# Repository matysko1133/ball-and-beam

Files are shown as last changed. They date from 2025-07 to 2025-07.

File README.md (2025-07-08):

> # Ball and Beam PID Controller
> Bachelor thesis - Positioning a Ball on an Inclined Beam Using Scilab Software
>
> The subject of this bachelor thesis is the design and implementation of a ball and inclined beam system using the Arduino UNO platform, an infrared ToF distance sensor and a servo actuator. The objective was to develop a control system that applies the principles of feedback control to ensure accurate and stable positioning of the ball through the controller’s control variable. The solution included the construction of the mechanical setup, system identification, synthesis and implementation of the PID controller in the Scilab environment and its interfacing with hardware components. The thesis also documents the design of ideal construction parts and the selection of a suitable ball. Based on experimental measurements, a mathematical model was created and the PID controller parameters were determined. The control algorithm was implemented on a physical system that initially exhibited unsatisfactory behavior. Therefore, the controller parameters were adjusted and finetuned again using the mathematical model.
>
> ## Startup guide
> This document serves as a guide to running simulations, whether with a model or with a real system. Certain steps are identical in both cases. It is necessary to have the necessary development environment **Arduino IDE (version 2.3.3)** and **Scilab software (version 2024.1.0)**. All scripts and simulation schemes that are necessary for the simulation alternative are attached in files.
> 
>> ### Running a simulation on the model
>>  To start a simulation with the model, it is necessary to load the parameters of the system and the PID controller.
>> Run the script *PID_parameters.sci*. After this step, in the file named
>> *model_PID_controller.zcos* just start the simulation by pressing the "Start" button, which is located
>> in the top bar of the window under the white arrow icon. After the simulations are finished, another click will appear on the screen
>> two windows with time courses of the measured quantities will appear. However, these waveforms can be displayed more clearly by running the script *model_plotter.sci*. The script
>> adds grids in the graphic outputs for better identification of critical points and legends describing individual.
> 
>> ### Running the simulation on a real system
>> Running on a real system includes specific steps that are required before the actual run. A special requirement is to upload the *toolbox_arduino_v5.ino* code to the Arduino UNO
>> board via the Arduino IDE environment. Without this script, it is not possible to establish the communication between Arduino and Scilab.
>> Equally important is the correct connection of the hardware components, specifically connecting the ToF sensor pin **SDA to the Arduino pin A4**, the **SCL pin to the A5 pin** and >> **the servo motor pin for the control signal (in our case the orange cable) to the Arduino digital pin
>> ~9 supporting PWM**. Since *toolbox_ardino_v5.ino* works with servomotor pins 9 and 10, it is possible to use the control signal also on pin 10, then it is necessary to be able to >> specify this change in the simulation scheme in the block **"Servo WRITE"** (1 represents pin 9, 2 represents pin 10). Finally, the key connection between the PC and Arduino is a
>> USB cable on the correct port, which is specified in Scilab by the **ARDUINO_SETUP** block. To identify the currently connected COM port, it is best to use the Arduino platform IDE: >> *Tools -> "Port: COMX"*, or a direct listing in the bottom bar of the window. After these steps, the simulation *real_system_PID_controller.zcos* is started in the same way as model >> simulation, while the time course of the measured quantities changes in real time. However, if for some reason the user wants to plot the data after the simulation is finished, they >> can do so using the *real_system_plotter.sci* script.

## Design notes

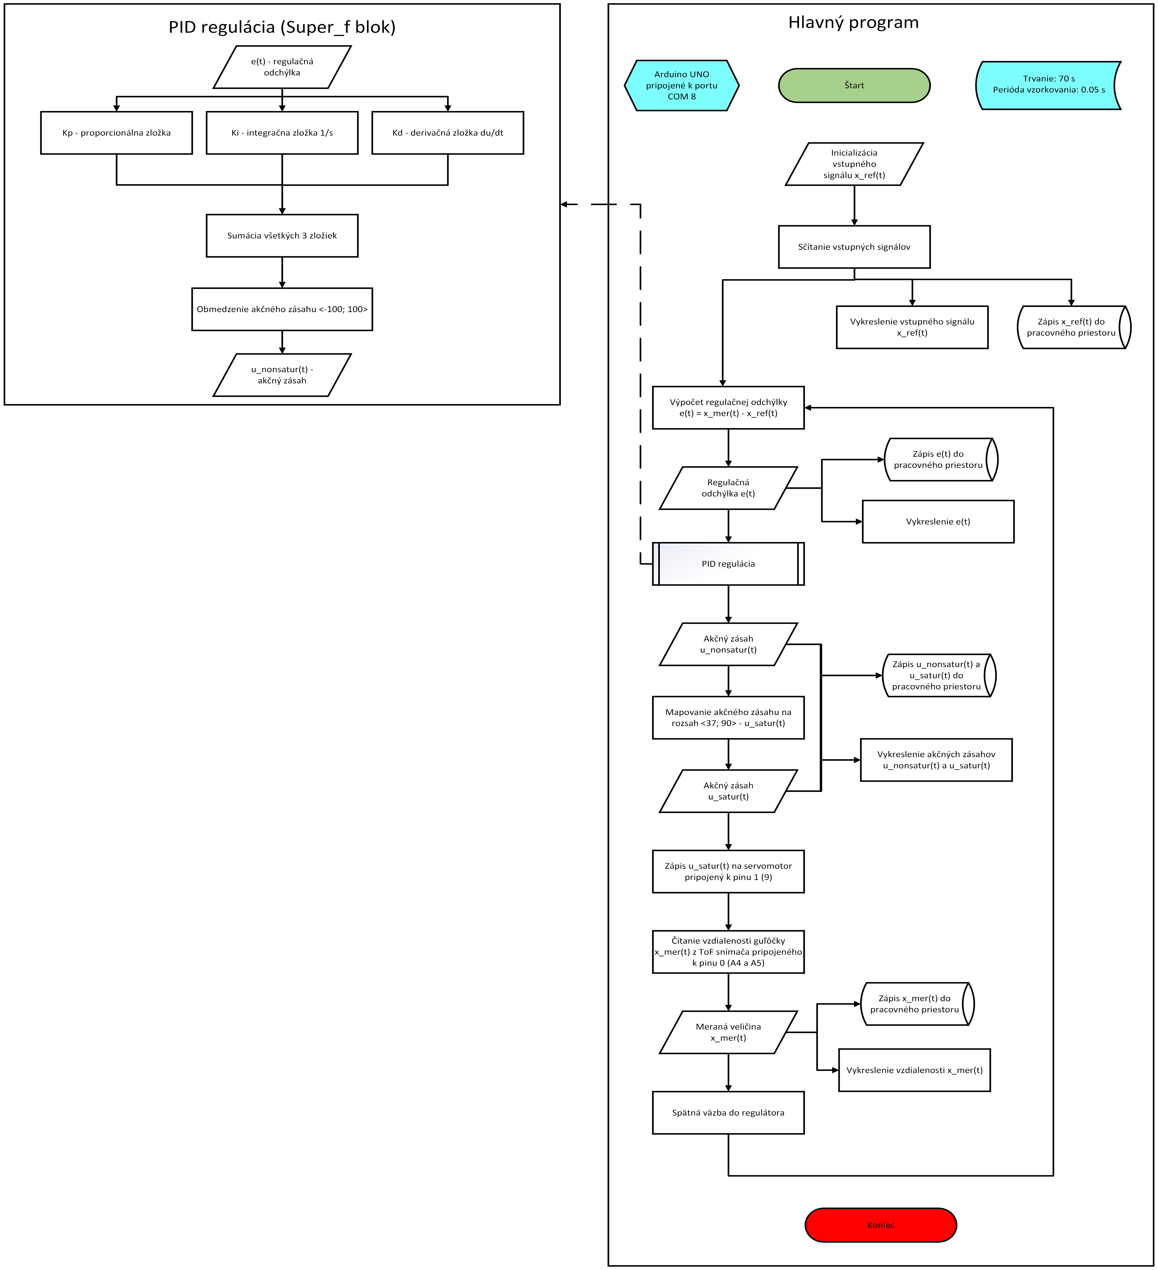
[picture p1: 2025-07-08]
flowchart.png

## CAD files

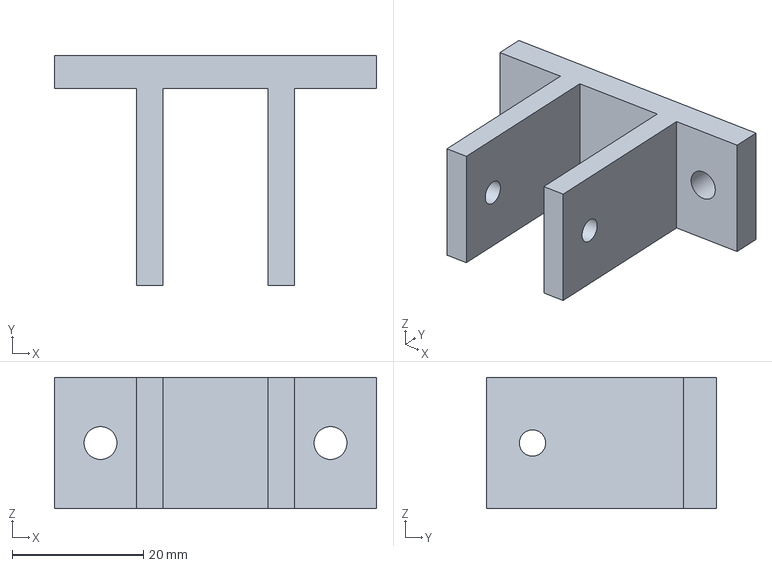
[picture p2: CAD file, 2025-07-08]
Construction/Part_4_top.FCStd
49.0 x 35.0 x 20.0 mm

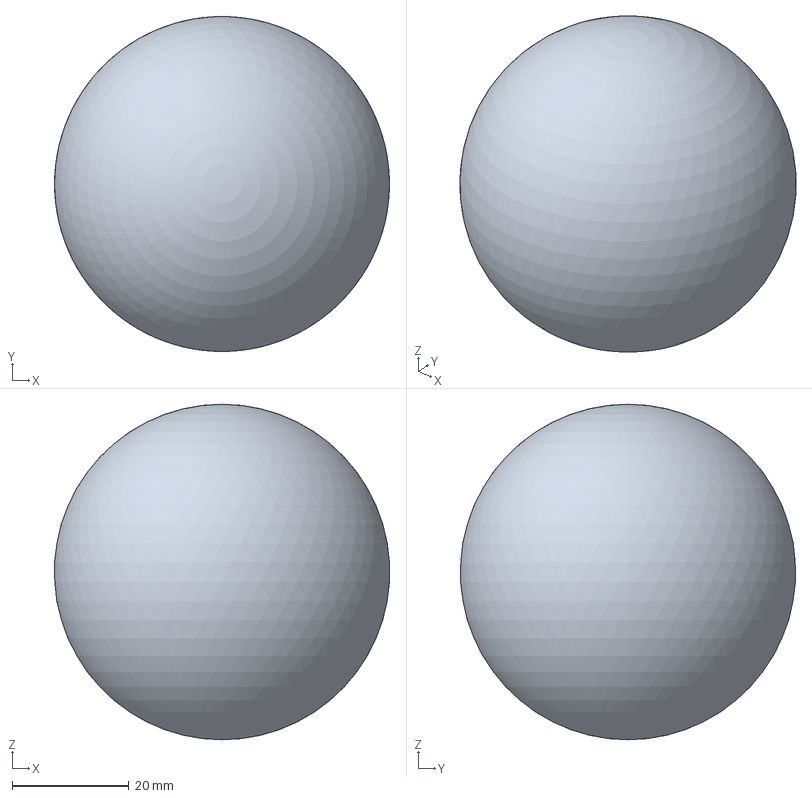
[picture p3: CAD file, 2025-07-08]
Construction/ball.FCStd
57.4 x 57.4 x 57.5 mm

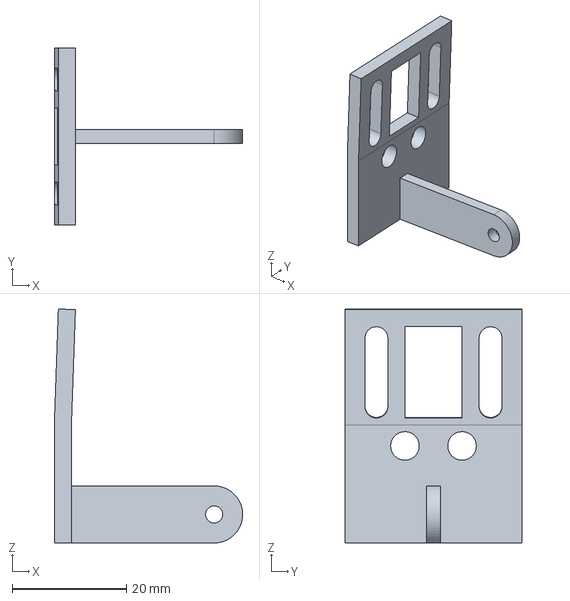
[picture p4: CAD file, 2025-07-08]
Construction/Part_5.FCStd
33.0 x 31.0 x 41.0 mm

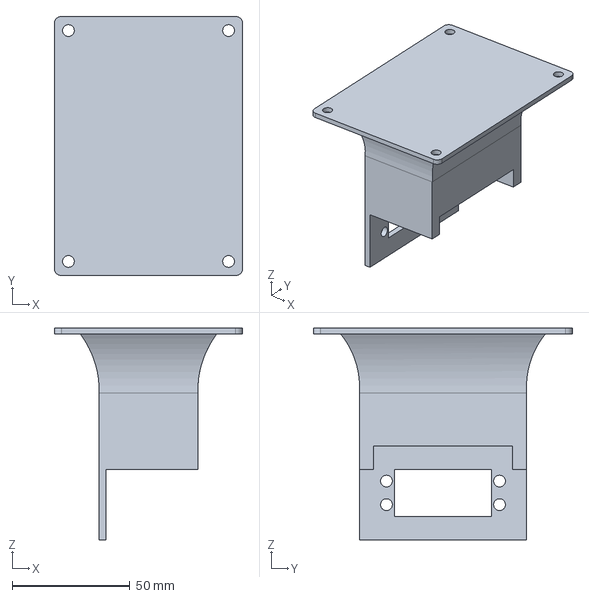
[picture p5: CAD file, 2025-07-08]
Construction/Part_3.FCStd
80.0 x 110.0 x 90.0 mm

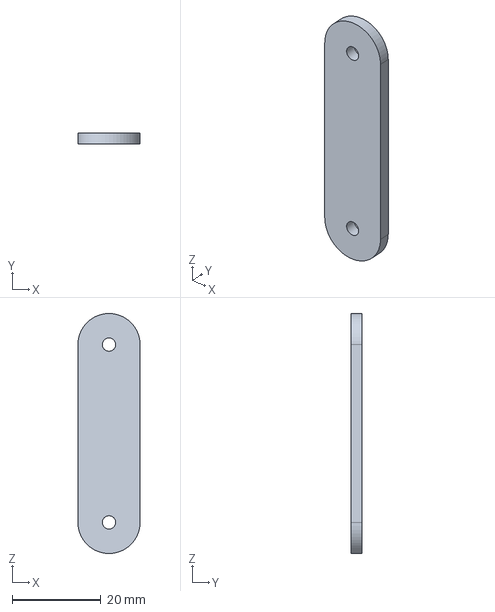
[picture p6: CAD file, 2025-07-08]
Construction/Part_1.FCStd
14.0 x 2.50 x 54.0 mm

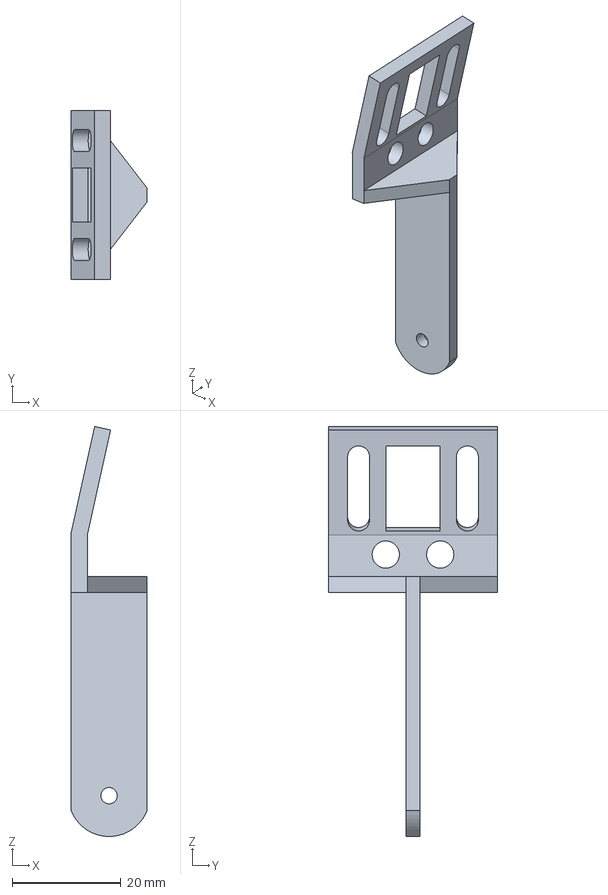
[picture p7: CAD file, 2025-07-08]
Construction/Part_1_5.FCStd
14.0 x 31.0 x 75.3 mm

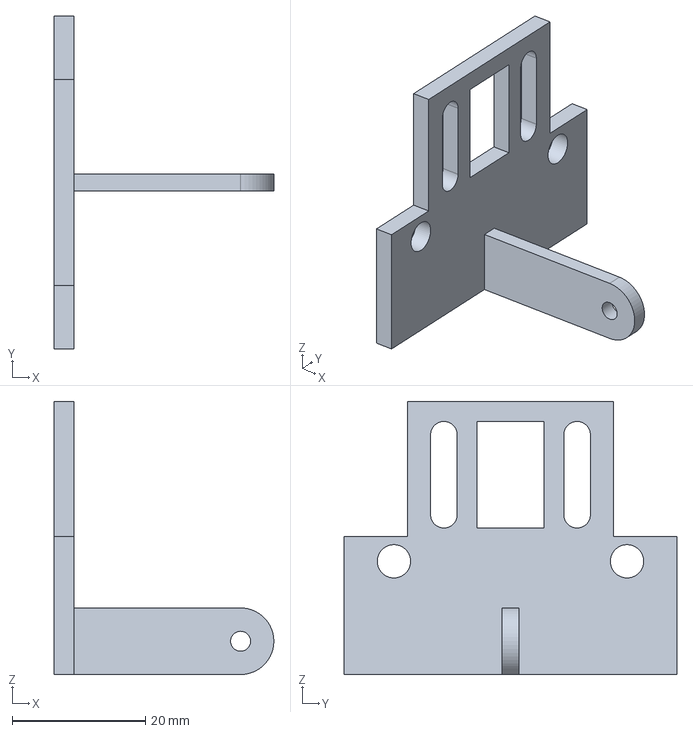
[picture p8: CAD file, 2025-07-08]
Construction/Part_5_rovny.FCStd
33.0 x 50.0 x 41.0 mm

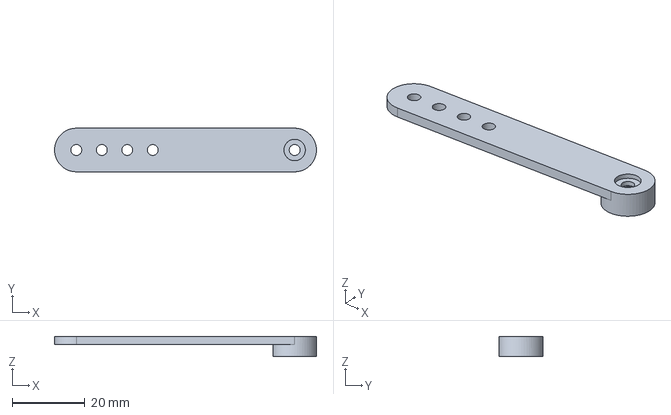
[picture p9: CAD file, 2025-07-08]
Construction/Part_2.FCStd
72.0 x 12.0 x 5.60 mm

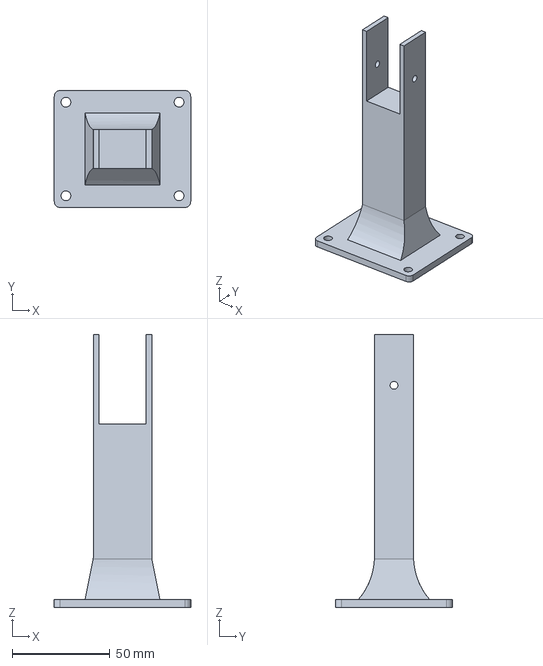
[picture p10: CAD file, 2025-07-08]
Construction/Part_4_edited.FCStd
70.0 x 60.0 x 140.0 mm

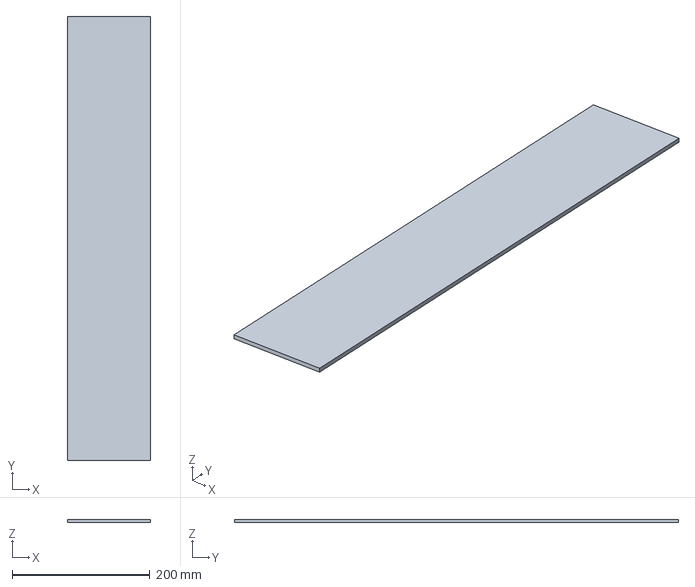
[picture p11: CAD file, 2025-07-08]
Construction/base.FCStd
120.0 x 645.0 x 5.00 mm

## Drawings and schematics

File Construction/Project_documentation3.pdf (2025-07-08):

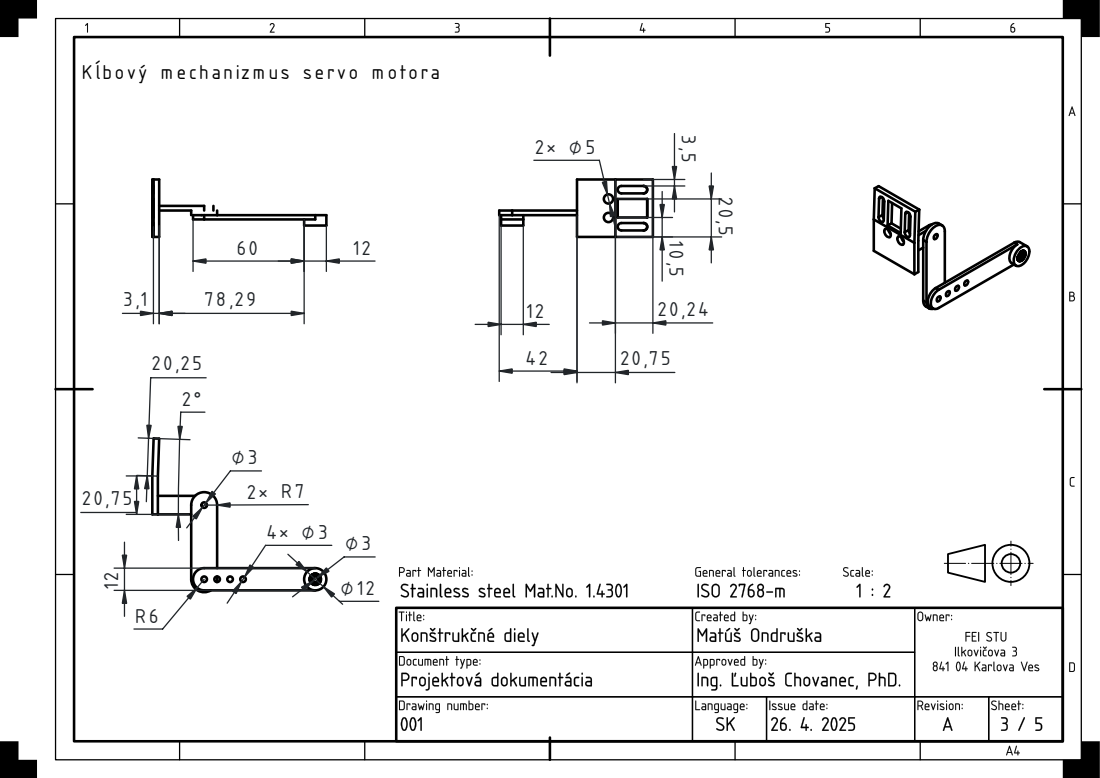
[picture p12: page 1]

K ĺbový m echanizm us servo m otora

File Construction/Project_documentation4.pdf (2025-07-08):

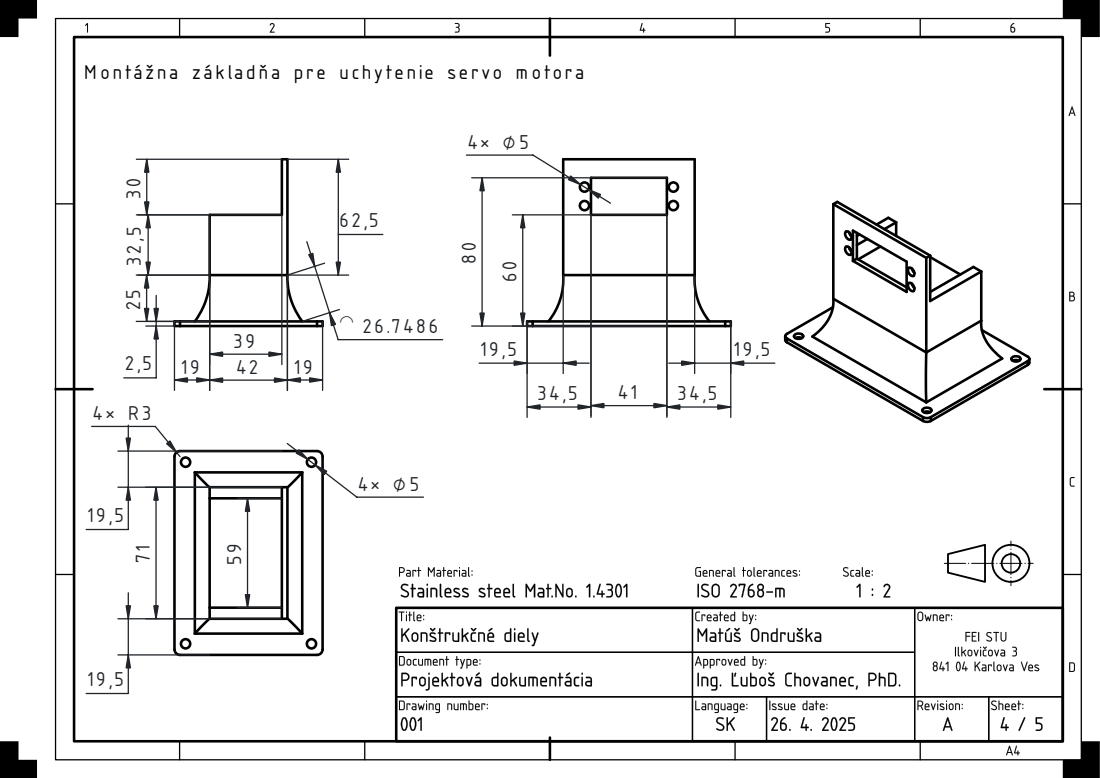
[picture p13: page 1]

M ontážna základňa pre uchytenie servo m otora

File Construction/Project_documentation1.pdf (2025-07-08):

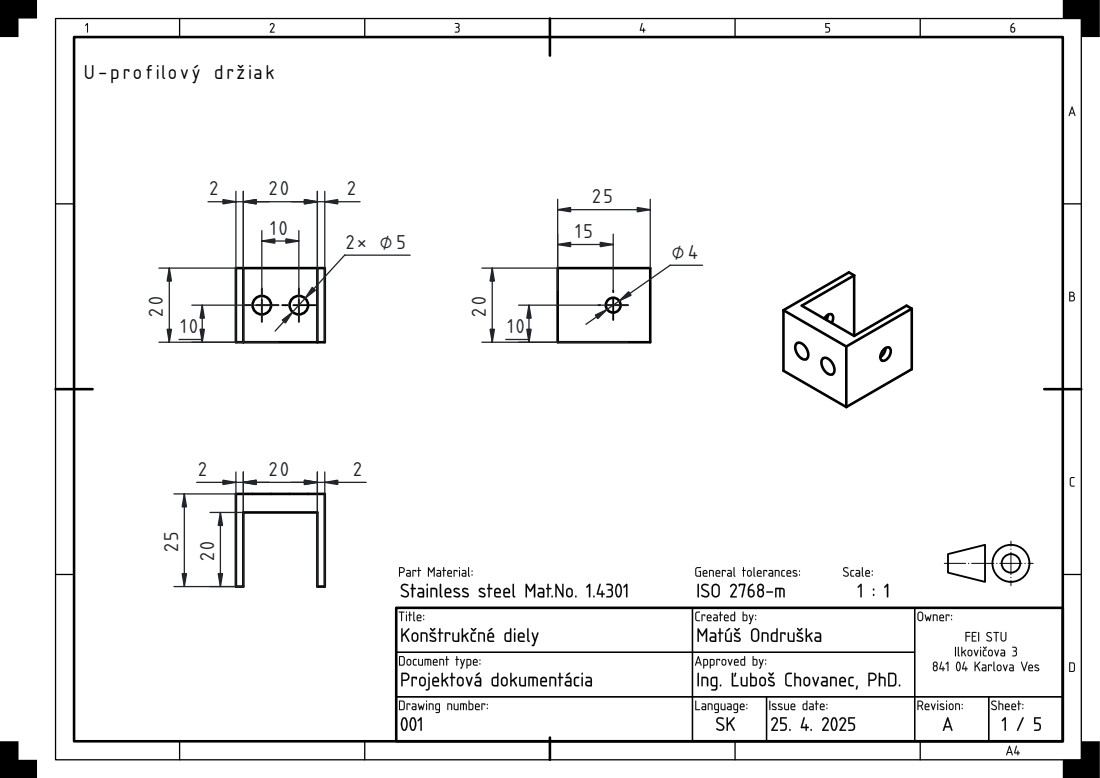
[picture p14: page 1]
U -profilový držiak

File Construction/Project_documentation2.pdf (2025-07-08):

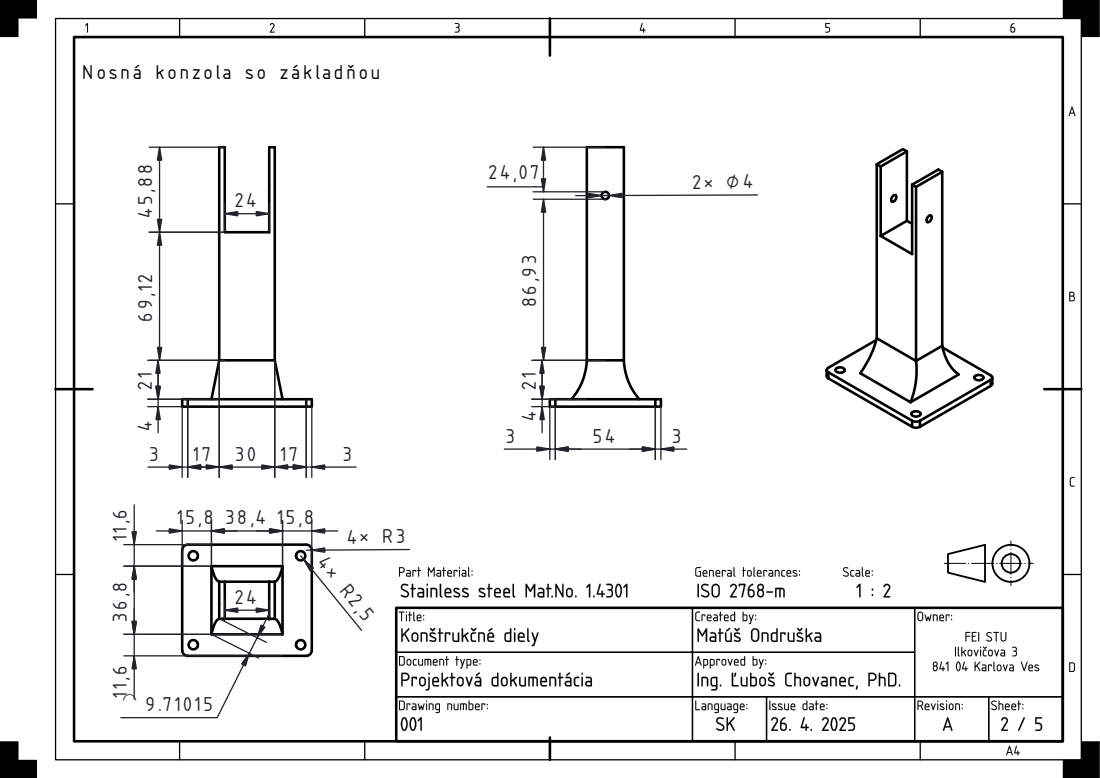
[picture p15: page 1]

N osná konzola so základňou

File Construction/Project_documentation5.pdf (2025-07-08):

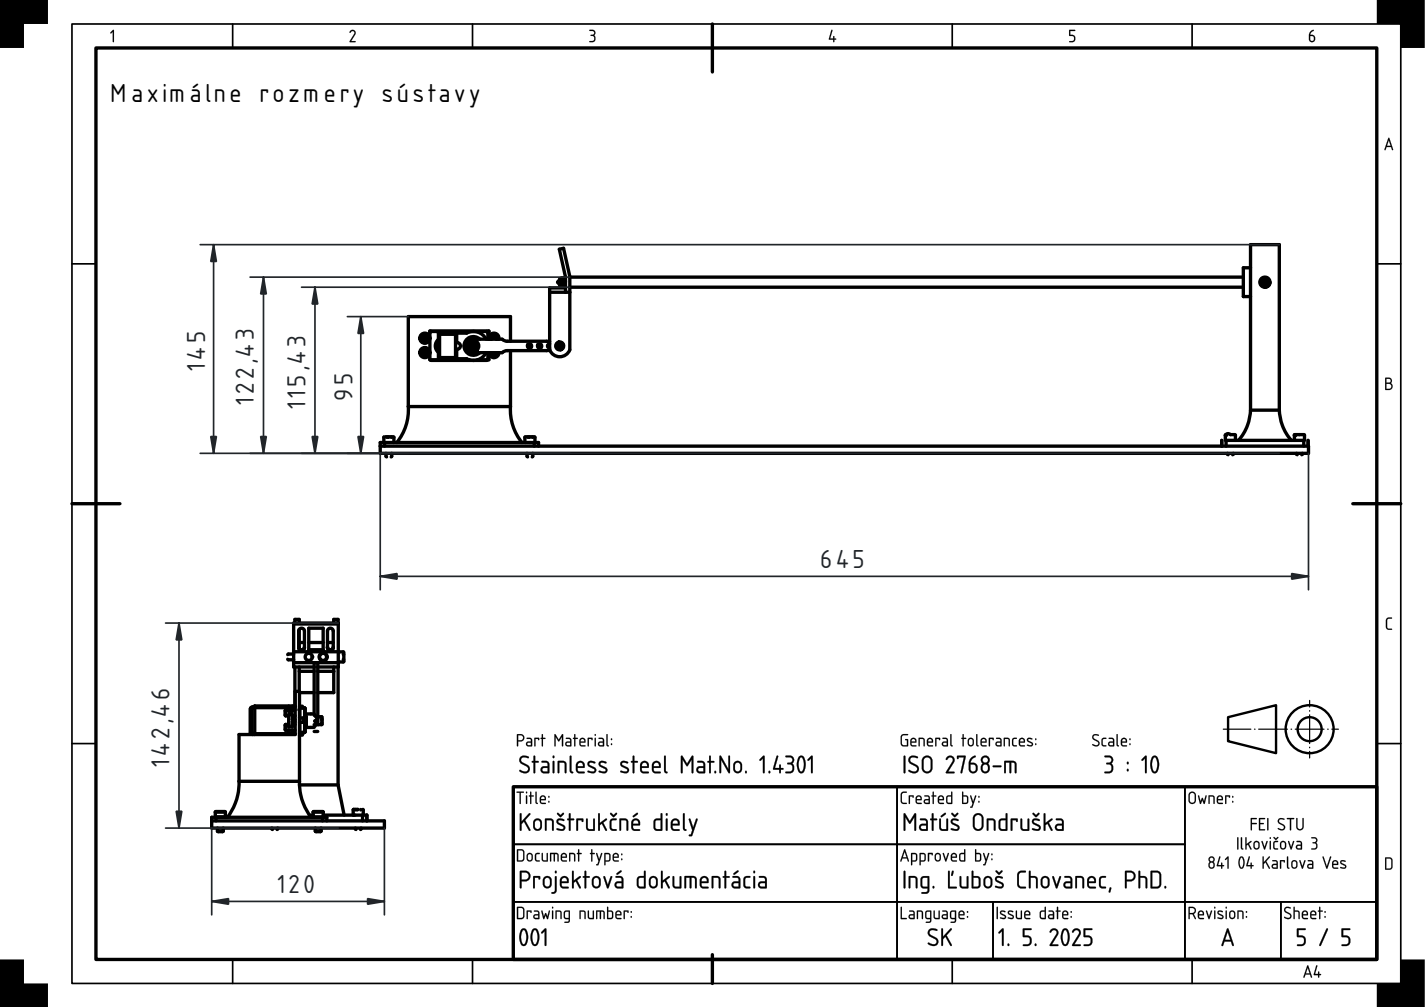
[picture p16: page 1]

M axim álne rozm ery sústavy

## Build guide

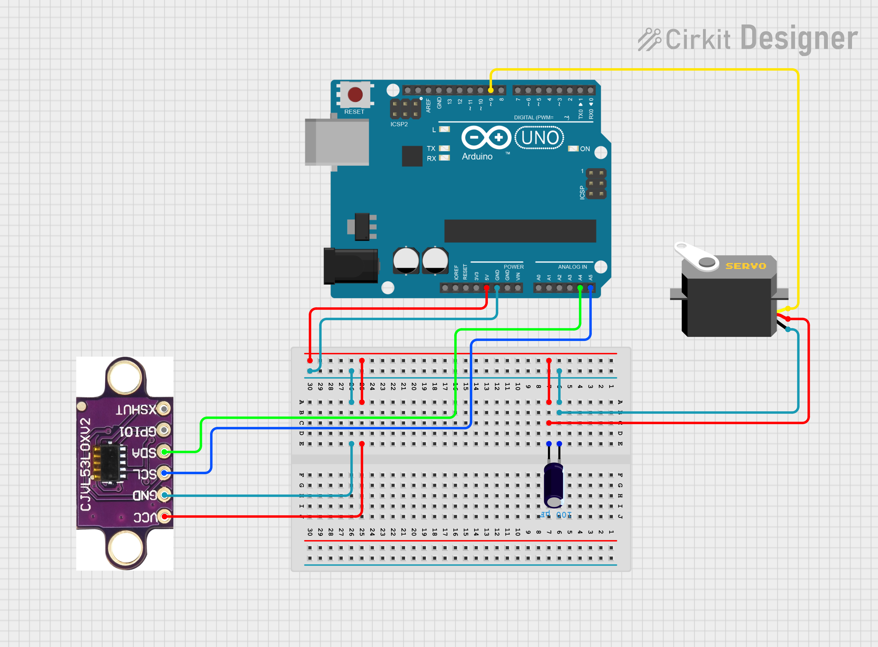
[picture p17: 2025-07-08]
circuit_wiring.png

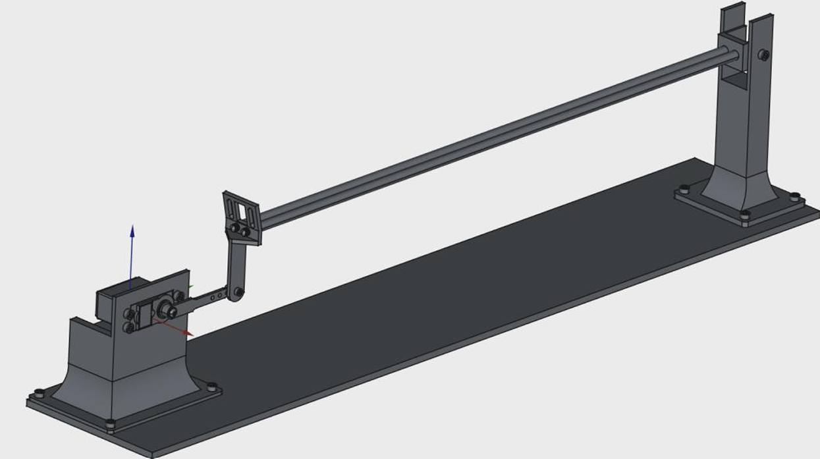
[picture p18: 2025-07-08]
Construction/full_construction.png

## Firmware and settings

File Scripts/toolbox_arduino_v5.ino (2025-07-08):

/* This file is meant to be used with the SCILAB arduino  
   toolbox, however, it can be used from the IDE environment
   (or any other serial terminal) by typing commands like:
   
   Conversion ascii -> number
   48->'0' ... 57->'9' 58->':' 59->';' 60->'<' 61->'=' 62->'>' 63->'?' 64->'@' 
   65->'A' ... 90->'Z' 91->'[' 92->'\' 93->']' 94->'^' 95->'_' 96->'`' 
   97->'a' ... 122->'z'
   
   Dan0 or Dan1 : attach digital pin n (ascii from 2 to b) to input (0) or output (1)
   Drn : read digital value (0 or 1) on pin n (ascii from 2 to b)
   Dwn0 or Dwn1 : write 1 or 0 on pin n
   An    : reads analog pin n (ascii from 0 to 19)
   Wnm  : write analog value m (ascii from 0 to 255) on pin n (ascii from 0 to 19)
   Sa1 or Sa2 : Attach servo 1 (digital pin 9) or 2 (digital pin 10)
   Sw1n or Sw2n : moves servo 1 or servo 2 to position n (from ascii(0) to ascii(180))
   Sd1 or Sd2 : Detach servo 1 or 2
   
   Generic DC_Motor
   Cijkl : setup for generic DCmotor number i (1 to 4), PW1 on pin number j, PWM2 or direction on pin number k, mode=l
           l=0 for L293 (2 PWM) and l=1 for L298 (1PWM + 1 bit for direction)
   Mijk  : sets speed for generic DCmotor number i, j=0/1 for direction, k=ascii(0) .. ascii(255)
   Mir   : releases motor i (r=release)

   Generic Interrupt counter
   Iai   : activate counter on INT number i (i=ascii(2 or 3 or 18 or 19 or 20 or 21)
   Iri   : release counter on INT number i
   Ipi   : read counter on INT number i
   Izi   : reset counter on INT number i

   MPU6050 acquisition
   Ga : launch acquisition
   Gs : stop acquisition
   Gr : read 9 data in the order yaw, pitch, roll, ax, ay, az, wx, wy ,wz

   Generic Encoder
   Eajkl: activate encoder on channelA on INT number j (j=ascii(2 or 3 or 18 or 19 or 20 or 21) et channelB on pin k or INT number k (k=ascii(0)..ascii(53))
           and l=1 or 2 or 4 for 1x mode (count every rising of chA) or 2x mode (count every change statement of chA)
           or  4x mode (every change statement of chA et chB)
   Eri   : release encoder on INTi
   Epi   : read position of encoder on INTi
   Ezi   : reset value of encoder on INTi position
   
   R0    : sets analog reference to DEFAULT
   R1    : sets analog reference to INTERNAL
   R2    : sets analog reference to EXTERNAL
   R3   : send version of the code
   */

#include <Servo.h>

#include <VL53L0X.h>
//#include <VL6180X.h>
#include "Wire.h"
#include "I2Cdev.h"
#include "MPU6050_6Axis_MotionApps20.h"

#define SCALING 1

MPU6050 mpu;
VL53L0X tof;
//VL6180X tof;

#define OUTPUT_READABLE_YAWPITCHROLL

/* define internal for the MEGA as 1.1V (as as for the 328)  */
#if defined(__AVR_ATmega1280__) || defined(__AVR_ATmega2560__)
#define INTERNAL INTERNAL1V1
#endif

/* create and initialize servos                              */
Servo servo1;
Servo servo2;

/* Generic motors */
int dcm1_pin1,dcm1_pin2,dcm1_mode;
int dcm2_pin1,dcm2_pin2,dcm2_mode;
int dcm3_pin1,dcm3_pin2,dcm3_mode;
int dcm4_pin1,dcm4_pin2,dcm4_mode;

// Generic encoder 
/* Encoders initialisation */
// volatile declare as those variables will change in interrupts
volatile long int encoder_0_position = 0,encoder_1_position = 0, encoder_2_position = 0, encoder_3_position = 0, encoder_4_position = 0, encoder_5_position = 0;
int encoder_0_int2 ;          // Pin used for encoder0 chanel B : define from scilab
int encoder_1_int2 ;          // Pin used for encoder1 chanel B : define from scilab
int encoder_2_int2 ;          // Pin used for encoder2 chanel B : define from scilab
int encoder_3_int2 ;          // Pin used for encoder3 chanel B : define from scilab
int encoder_4_int2 ;          // Pin used for encoder4 chanel B : define from scilab
int encoder_5_int2 ;          // Pin used for encoder5 chanel B : define from scilab
int encoder_num, encoder_int2;
int corresp[7]={0,2,3,21,20,19,18}; //Correspondance beetween interrupt number and pin number, v5 added a dummy 0 as workaround for ascii 0 issue for scilab

//Generic counter
volatile long int counter_0=0,counter_1=0,counter_2=0,counter_3=0,counter_4=0,counter_5=0;

int initiat=1;


// MPU control/status vars
bool dmpReady = false;  // set true if DMP init was successful
uint8_t mpuIntStatus;   // holds actual interrupt status byte from MPU
uint8_t devStatus;      // return status after each device operation (0 = success, !0 = error)
uint16_t packetSize;    // expected DMP packet size (default is 42 bytes)
uint16_t fifoCount;     // count of all bytes currently in FIFO
uint8_t fifoBuffer[64]; // FIFO storage buffer
bool acq_launched = false; //boolean used to launch acquisition
// orientation/motion vars
Quaternion q;           // [w, x, y, z]         quaternion container
VectorInt16 aa;         // [x, y, z]            accel sensor measurements
VectorInt16 aaReal;     // [x, y, z]            gravity-free accel sensor measurements
VectorInt16 aaWorld;    // [x, y, z]            world-frame accel sensor measurements
VectorInt16 w;          // [x, y, z]            world-frame gyroscope sensor measurements
VectorFloat gravity;    // [x, y, z]            gravity vector
float euler[3];         // [psi, theta, phi]    Euler angle container
float pr[2];           // [pitch, roll]   pitch/roll container
float ypr[3];           // [pitch, roll]   pitch/roll container

int data[9];  // lacet, tangage, roulis, ax, ay, az, wx, wy, wz

bool init_mpu=false;

// ================================================================
// ===               INTERRUPT DETECTION ROUTINE                ===
// ================================================================

volatile bool mpuInterrupt = false;     // indicates whether MPU interrupt pin has gone high
void dmpDataReady() {
    mpuInterrupt = true;
}


void setup() {
  /* initialize serial                                       */
  Serial.begin(115200);

     ////////////////////////////
    //only if MPU6050 is used
    /////////////////////////////
   // join I2C bus (I2Cdev library doesn't do this automatically)
    Wire.begin();
    tof.setTimeout(500);
    if (!tof.init()) {
      Serial.println("VL53L0X init failed!");
    } else {
      tof.startContinuous();
    }
    /*tof.init();
    tof.configureDefault();
    tof.setScaling(SCALING);

    tof.writeReg(VL6180X::SYSRANGE__MAX_CONVERGENCE_TIME, 30);
    tof.writeReg16Bit(VL6180X::SYSALS__INTEGRATION_PERIOD, 50);

    tof.setTimeout(500);
    tof.stopContinuous();
    delay(300);
    tof.startInterleavedContinuous(100);*/

    while (!Serial);
    mpu.initialize();
    while (Serial.available() && Serial.read()); // empty buffer
    //while (!Serial.available());                 // wait for data
    //while (Serial.available() && Serial.read()); // empty buffer again

    devStatus = mpu.dmpInitialize();
    
    if (devStatus == 0) {
        mpu.setDMPEnabled(true);
        attachInterrupt(0, dmpDataReady, RISING);
        mpuIntStatus = mpu.getIntStatus();
        dmpReady = true;
        packetSize = mpu.dmpGetFIFOPacketSize();
        
        init_mpu=true;
    } 
    else {
        init_mpu=false;
    }
}

void loop() {
  
  /* variables declaration and initialization                */
  
  static int  s   = -1;    /* state                          */
  static int  pin = 13;    /* generic pin number             */
  static int  dcm =  4;    /* generic dc motor number        */

  int  val =  0;           /* generic value read from serial */
  //int  agv =  0;           /* generic analog value           */
  int  dgv =  0;           /* generic digital value          */
  static int  enc   = 1;    /* encoder number 1 (or 2 for Arduino mega)     */

 if (true){
  get_data_MPU6050();
 }
  if (Serial.available()!=0) {
    val = Serial.read(); 
  };
  
  //while (Serial.available()==0) {}; // Waiting char
  //val = Serial.read(); 
  
//  if (val==0){// version
//    Serial.print('v3');
//    val=-1;
//  }
  //case A -> Analog
  if (val==65){//A -> Analog read
    while (Serial.available()==0) {}; // Waiting char
//    val=Serial.read();
//    if (val==114){ //'r'-> read pin
//       while (Serial.available()==0) {}; // Waiting char
       val=Serial.read();
       if (val>47 && val<67) { //from pin 0, to pin 19
          pin=val-48; //number of the pin
          uint16_t agv = tof.readRangeContinuousMillimeters();
          //Serial.println(agv);
          //Serial.print(agv);
          Serial.write((uint8_t*)&agv,2); /* send binary value via serial  */   
       }
       val=-1;
  }
  else if (val==87){//W -> Analog write
      while (Serial.available()==0) {}; // Waiting char
      val=Serial.read();
         if (val>47 && val<67) { //from pin 0 to pin 19
            pin=val-48; //number of the pin
            while (Serial.available()==0) {}; // Waiting char
            val=Serial.read();
            analogWrite(pin,val);
         }
          val=-1;
      }
  //}

  //case D -> Digital
  else if (val==68){//D -> Digital pins
    while (Serial.available()==0) {}; // Waiting char
    val=Serial.read();
    if (val==97){ //'a'-> declare pin
       while (Serial.available()==0) {}; // Waiting char
       val=Serial.read();
       if (val>49 && val<102) {
         pin=val-48;
         while (Serial.available()==0) {}; // Waiting char
         val=Serial.read();
         if (val==48 || val==49) { 
            if (val==48){//'0' -> input
               pinMode(pin,INPUT);
            }
            else if (val==49){//'1' -> output
               pinMode(pin,OUTPUT);
            }
         }
       }
    }
    if (val==114){ //'r'-> read pin
       while (Serial.available()==0) {}; // Waiting char
       val=Serial.read();
       if (val>49 && val<102) { 
          pin=val-48; //number of the digital pin
          dgv=digitalRead(pin);      
//          Serial.println(dgv);        
          Serial.print(dgv);         
       }
    }
    if (val==119){ //'w'-> write pin
       while (Serial.available()==0) {}; // Waiting char
       val=Serial.read();
       if (val>49 && val<102) { 
          pin=val-48; //number of the digital pin
          while (Serial.available()==0) {}; // Waiting char
          val=Serial.read();
          if (val==48 || val==49) { // 0 or 1
            dgv=val-48;
            digitalWrite(pin,dgv);
//            Serial.println(dgv);    
          }
       }
    }
   val=-1;

  }
  
  //case S -> servomotor
  else if (val==83){
    while (Serial.available()==0) {}; // Waiting char
    val=Serial.read();
    if (val==97){ //'a'-> declare servo
       while (Serial.available()==0) {}; // Waiting char
       val=Serial.read();
       if (val==49 || val==50) { //servo 1 or 2
          pin=val-48; //number of the servo
          if (pin==1) {
            servo1.attach(9); 
            servo1.write(0);           
//            agv=servo1.read();
//            Serial.println(agv);
          }
          if (pin==2) {
            servo2.attach(10); 
            servo2.write(0);           
//            agv=servo2.read();
//            Serial.println(agv);
          }

       }
    }
    if (val==100){ //'d'-> detach servo
       while (Serial.available()==0) {}; // Waiting char
       val=Serial.read();
       if (val==49 || val==50) { //servo 1 or 2
          pin=val-48; //number of the servo
          if (pin==1) {servo1.detach(); }
          if (pin==2) {servo2.detach(); }
       }
    }
    if (val==119){ //'w'-> write pin
       while (Serial.available()==0) {}; // Waiting char
       val=Serial.read();
       if (val==49 || val==50) { //servo 1 or 2
          pin=val-48; //number of the servo
          while (Serial.available()==0) {}; // Waiting char
          val=Serial.read();
          if (val>=0 && val<=180){
              if (pin==1) {
                servo1.write(val);
//                agv=servo1.read();
//                Serial.println(agv);
              }
              if (pin==2) {
                servo2.write(val);
//                agv=servo2.read();
//                Serial.println(agv);
              }
          }
       }
    }
   val=-1;

  }
  //case G -> deal with MPU6050
  else if (val==71){
    while (Serial.available()==0) {}; // Waiting char
      val=Serial.read();
      if (val==116){ //t = test if initialisation is ok
        if (init_mpu==true) Serial.print("OK");
        else Serial.print("KO");
      }
      if (val==97) { //a = activation (acquisition is launched)
        acq_launched= true;
        val=-1;
      }      
      if (val==114) { //r = read
        //get_data_MPU6050();
        if(false){
        for(int d=0;d<9;d++){
          Serial.print(data[d]);
          Serial.print(" ; ");
        }
        Serial.println(" fin");
        }
        else{
              Serial.write((uint8_t*) &data,2*9);
              /*Serial.write((uint8_t*) &ypr,3*4);
              Serial.write((uint8_t*)&aa.x,2);
              Serial.write((uint8_t*)&aa.y,2);
              Serial.write((uint8_t*)&aa.z,2);             
              Serial.write((uint8_t*)&w.x,2);                
              Serial.write((uint8_t*)&w.y,2);
              Serial.write((uint8_t*)&w.z,2); */
        }
        
        
        val=-1;
        
      }
      if (val==115) { //s = stop (acquisition is stopped)
        acq_launched= false;
        val=-1;
      }
        
  }
  //case I -> Interrupt
  else if (val==73){
      /* ASKING ACTIVATION OF AN COUNTER     */
      while (Serial.available()==0) {}; // Waiting char
      val=Serial.read();                                
      if (val==97) { //a = activation
         while (Serial.available()==0) {};                 // Waiting char
         val=Serial.read();                                // Read int_number (must be 0 or 1 on UNO / 1 to 5 on MEGA) : int_number set to encoder number
         pinMode(corresp[val],INPUT);              // set interrupt pin as input
         if       (val == 0) {attachInterrupt(val, counter_0_change, RISING);counter_0=0;}  //counter INT0
         else if  (val == 1) {attachInterrupt(val, counter_1_change, RISING);counter_1=0;}  //counter INT1
         else if  (val == 2) {attachInterrupt(val, counter_2_change, RISING);counter_2=0;}  //counter INT2
         else if  (val == 3) {attachInterrupt(val, counter_3_change, RISING);counter_3=0;}  //counter INT3
         else if  (val == 4) {attachInterrupt(val, counter_4_change, RISING);counter_4=0;}  //counter INT4
         else if  (val == 5) {attachInterrupt(val, counter_5_change, RISING);counter_5=0;}  //counter INT5
      }
      /* ASKING POSITION OF A COUNTER     */ 
      if (val==112) { //p = sending counting value
         while (Serial.available()==0) {};   // Waiting char
         val = Serial.read()   ;             //reading next value = counter number
         if      (val==0){ Serial.write((uint8_t*)&counter_0,4); }// asking counter 0 
         else if (val==1){ Serial.write((uint8_t*)&counter_1,4); }// asking counter 1 
         else if (val==2){ Serial.write((uint8_t*)&counter_2,4); }// asking counter 2 
         else if (val==3){ Serial.write((uint8_t*)&counter_3,4); }// asking counter 3 
         else if (val==4){ Serial.write((uint8_t*)&counter_4,4); }// asking counter 4 
         else if (val==5){ Serial.write((uint8_t*)&counter_5,4); }// asking counter 5 
     }
      /* ASKING RELEASE OF AN INTERRUPT   */ 
      if (val==114) { //r = release counter 
         while (Serial.available()==0) {};        // Waiting char
         val = Serial.read();                     //reading next value = counter number
         detachInterrupt(val);                    // Detach interrupt on chanel A of counter num=val
         if (val==0)       { counter_0=0;}        // Reset counter
         else if (val==1)  { counter_1=0;}        // Reset counter
         else if (val==2)  { counter_2=0;}        // Reset counter
         else if (val==3)  { counter_3=0;}        // Reset counter
         else if (val==4)  { counter_4=0;}        // Reset counter
         else if (val==5)  { counter_5=0;}        // Reset counter
      }
      /* ASKING RESET VALUE OF AN COUNTER     */ 
      if (val==122) { //z set to zero
         while (Serial.available()==0) {};        // Waiting char
         val = Serial.read();                     //reading next value = counter number
         if (val==0)       { counter_0=0;}        // Reset counter
         else if (val==1)  { counter_1=0;}        // Reset counter
         else if (val==2)  { counter_2=0;}        // Reset counter
         else if (val==3)  { counter_3=0;}        // Reset counter
         else if (val==4)  { counter_4=0;}        // Reset counter
         else if (val==5)  { counter_5=0;}        // Reset counter
       }
    val=-1;
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
